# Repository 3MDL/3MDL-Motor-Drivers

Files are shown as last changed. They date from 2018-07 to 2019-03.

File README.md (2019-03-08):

# About #

This repository contains design files for low-cost brushed DC motor drivers. These low-cost motor drivers were concieved for use in low-cost swarm robotics. Work was done under the Mechanism, Mobility, and Multifunctional Design Laboratory (3MDL) at the University of Toledo.

## In This Repository ##

The Firmware sub folder contains test code that was used to evaluate motor drivers that were based on microcontrollers.

The Hardware sub folder contains hardware design files for:
* An OP Amp based current regulator motor driver
    * This design was confirmed to work and the cost is marginally lower than the off the shelf driver IC solution. However, due to complex timing, only limited testing was performed before the motor driver failed due to shoot through in the H bridge circuit.
* A Microcrocontroller based current regulator motor driver
    * The footprint used for the microcntroller was incorrect so this design could not be evaluated
* A motor driver using an off the shelf motor driver IC
    * This design was confirmed to work, however near the current limit rating of the driver IC, additional cooling is required or else the driver IC goes into over temperature protection mode.

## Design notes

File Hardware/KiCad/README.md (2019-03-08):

# KiCad Repository Info #

KiCad Modules are located in the MOD sub folder

KiCad Library parts are located in the LIB sub folder

Library and Modules used here are common with the [Thunkit Electronics KiCad Repository](https://github.com/cmccaskey/THUNKIT-KICAD)

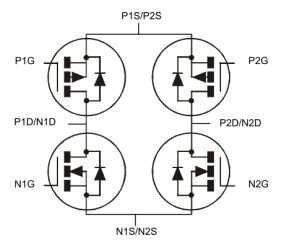
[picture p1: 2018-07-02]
Hardware/KiCad/MOD/DMHC3025LSD.png

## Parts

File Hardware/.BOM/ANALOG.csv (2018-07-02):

Id | Designator | Package | Quantity | Designation | Supplier and ref
1 | ,,,,,,,,,,,,,,,,,,,,,,,,,,,,,,,,,,,, | GND VIA | 37
2 | Q1,Q1,Q1 | SOIC-8_3.9x4.9mm_Pitch1.27mm | 3 | DMHC3025LSD
3 | C3,C4 | C_0603 | 2 | 10n
4 | P2,P5 | 100MIL_ST | 2 | PWR
5 | P3 | 100MIL_ST | 1 | VREF
6 | P4 | 100MIL_ST | 1 | DIR
7 | R1,R2,R3,R4,R5,R6,R7,R8,R11,R12 | R_0603 | 10 | 10K
8 | R9,R10 | R_0603 | 2 | 1K
9 | R13 | R_1812 | 1 | R
10 | U1 | SOIC-14_3.9x8.7mm_Pitch1.27mm | 1 | LM324
11 | U2 | SOIC-14_3.9x8.7mm_Pitch1.27mm | 1 | LM339
12 | P1 | 100MIL_ST | 1 | MOTOR
13 | C1,C2 | C_0603 | 2 | 0.1uF
14 | P6 | 100MIL_ST | 1 | PWM
15 | R14,R15 | R_0603 | 2 | 150

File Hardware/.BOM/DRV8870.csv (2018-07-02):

Id | Designator | Package | Quantity | Designation | Supplier and ref
1 | ,,,,,,,,, | GND VIA | 10
2 | U1 | HTSOP-8-1EP_3.9x4.9mm_Pitch1.27mm | 1 | DRV8870
3 | C1 | CP_Elec_6.3x7.7 | 1 | 47u
4 | C2 | C_0603 | 1 | 0.1u
5 | P1 | 100MIL_ST | 1 | PWR
6 | P2 | 100MIL_ST | 1 | DIR
7 | P3 | 100MIL_ST | 1 | VREF
8 | P4 | 100MIL_ST | 1 | MOTOR
9 | R1 | R_1812 | 1 | 0.1
Id | Designator | Package | Quantity | Designation | Supplier and ref
1 | ,,,,,,,,,,,,,,,, | GND VIA | 17
2 | C1 | C_0603 | 1 | 0.1uF
3 | C2,C3 | C_0603 | 2 | 22pF
4 | IC1 | QFN-24-1EP_4x4mm_Pitch0.5mm | 1 | ATTINY24A-M
5 | P1 | 100MIL_ST | 1 | MOTOR
6 | P2 | 100MIL_ST | 1 | VREF
7 | P3,P4 | 100MIL_ST | 2 | POWER
8 | P5 | Pin_Header_Straight_2x03_Pitch2.54mm | 1 | ICSP
9 | Q1 | SOIC-8_3.9x4.9mm_Pitch1.27mm | 1 | DMHC3025LSD
10 | Q2,Q3 | SOT-23 | 2 | Q_NMOS_DGS
11 | R1,R3,R4,R5 | R_0603 | 4 | 1K
12 | R2 | R_1812 | 1 | R
13 | Y1 | Crystal_HC49-U_Vertical | 1 | Crystal
Id | Designator | Package | Quantity | Designation | Supplier and ref
1 | ,,,,,,,,,,,,,,,,,,,,,,,,,,,,,,,,,,,, | GND VIA | 37
2 | Q1,Q1,Q1 | SOIC-8_3.9x4.9mm_Pitch1.27mm | 3 | DMHC3025LSD
3 | C3,C4 | C_0603 | 2 | 10n
4 | P2,P5 | 100MIL_ST | 2 | PWR
5 | P3 | 100MIL_ST | 1 | VREF
6 | P4 | 100MIL_ST | 1 | DIR
7 | R1,R2,R3,R4,R5,R6,R7,R8,R11,R12 | R_0603 | 10 | 10K
8 | R9,R10 | R_0603 | 2 | 1K
9 | R13 | R_1812 | 1 | R
10 | U1 | SOIC-14_3.9x8.7mm_Pitch1.27mm | 1 | LM324
11 | U2 | SOIC-14_3.9x8.7mm_Pitch1.27mm | 1 | LM339
12 | P1 | 100MIL_ST | 1 | MOTOR
13 | C1,C2 | C_0603 | 2 | 0.1uF
14 | P6 | 100MIL_ST | 1 | PWM
15 | R14,R15 | R_0603 | 2 | 150

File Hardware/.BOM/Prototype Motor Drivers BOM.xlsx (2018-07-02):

Designation | Kicad Package | Quantity | Digikey PN
0.05 Ohm Resistor | R_1812 | 10 | P50NBCT-ND
150 Ohm Resistor | R_0603 | 10 | RNCP0603FTD150RCT-ND
22pF Ceramic Capacitor | C_0603 | 10 | 732-7748-1-ND
10n Ceramic Capacitor | C_0603 | 10 | 732-7933-1-ND
0.1u Ceramic Capacitor | C_0603 | 10 | Can’t Find
47u Electrolytic Capacitor | CP_Elec_6.3x7.7 | 3 | PCE3908CT-ND
DMHC3025LSD MOSFET (H-Bridge) | SOIC-8_3.9x4.9mm_Pitch1.27mm | 10 | DMHC3025LSD-13DICT-ND
Q_NMOS_DGS MOSFET (NMOS) | SOT-23 | 10 | 2N7002-FDICT-ND
DRV8870 Motor Driver | HTSOP-8-1EP_3.9x4.9mm_Pitch1.27mm | 3 | 296-42660-1-ND
LM324 OP-Amp | SOIC-14_3.9x8.7mm_Pitch1.27mm | 3 | 497-1580-1-ND
LM339 Comparator | SOIC-14_3.9x8.7mm_Pitch1.27mm | 3 | 296-1013-1-ND
ATTINY24A-M Microcontroller | QFN-24-1EP_4x4mm_Pitch0.5mm | 3 | ATTINY24A-MURCT-ND

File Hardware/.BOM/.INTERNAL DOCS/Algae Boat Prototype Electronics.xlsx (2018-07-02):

M.I.M.E. Purchase Request
 | THE UNIVERSITY OF TOLEDO
 | Nitschke Hall Room 4005
 | Toledo, Ohio 43606 PH: (419) 530-8210 FAX: (419)-530-8206
 | ATTN: M.I.M.E. Budget Office
VENDOR: |  | Digi-Key |  |  | DATE: | 2018-07-02
ADDR 1: |  | 701 Brooks Avenue South
ADDR 2: |  |  |  |  | ACCOUNT # ITEMS WILL BE
C/S/Z: |  | Thief River Falls, MN 56701 |  |  | CHARGED TO: | 110780
PH: |  | 218-681-6674 |  |  | PICKUP or
FAX: |  |  |  |  | DELIVERY | Deliver
 | QUANTITY | CATALOG # | AND DESCRIPTION OF MATERIALS |  | Unit Cost | Total Cost
 | 10 | P50NBCT-ND | 0.05 Ohm Resistor |  | $0.63 | $6.32
 | 10 | RNCP0603FTD150RCT-ND | 150 Ohm Resistor |  | $0.03 | $0.30
 | 10 | 732-7748-1-ND | 22pF Ceramic Capacitor |  | $0.03 | $0.25
 | 10 | 732-7933-1-ND | 10n Ceramic Capacitor |  | $0.02 | $0.21
 | 3 | PCE3908CT-ND | 47u Electrolytic Capacitor |  | 0.38 | $1.14
 | 10 | DMHC3025LSD-13DICT-ND | DMHC3025LSD MOSFET (H-Bridge) |  | 0.912 | $9.12
 | 10 | 2N7002-FDICT-ND | Q_NMOS_DGS MOSFET (NMOS) |  | 0.163 | $1.63
 | 3 | 296-42660-1-ND | DRV8870 Motor Driver |  | 1.94 | $5.82
 | 3 | 497-1580-1-ND | LM324 OP-Amp |  | 0.36 | $1.08
 | 3 | 296-1013-1-ND | LM339 Comparator |  | 0.36 | $1.08
 | 3 | ATTINY24A-MURCT-ND | ATTINY24A-M Microcontroller |  | 0.76 | $2.28
 |  | Notes:
 |  |  | Shipping and Handling Charges
 |  |  |  | AUTOMATIC TOTAL WILL BE ENTERED |  | $29.23
* | Purchases under $2,500 can be faxed directly from the dept. budget office to the vendor.
* | Purchases over $2,500 need to be submitted to Purchasing via the dept. budget office.
* | Purchases that are grant related and over $2,000 must be approvaed by Grants Accounting via the dept. budget office.
* | Purchases that are over $10,000.00 need to go through bidding process via the dept. budget office.
 | Please complete all necessary information
 | in the areas above for all on or off campus |  |  | SUBMITTED BY:
 | purchase requests. Please e-mail the attached |  |  | Cameron McCaskey
 | form to kathryn.rose@utoledo.edu. Orders
 | will be processed the same day of receipt.

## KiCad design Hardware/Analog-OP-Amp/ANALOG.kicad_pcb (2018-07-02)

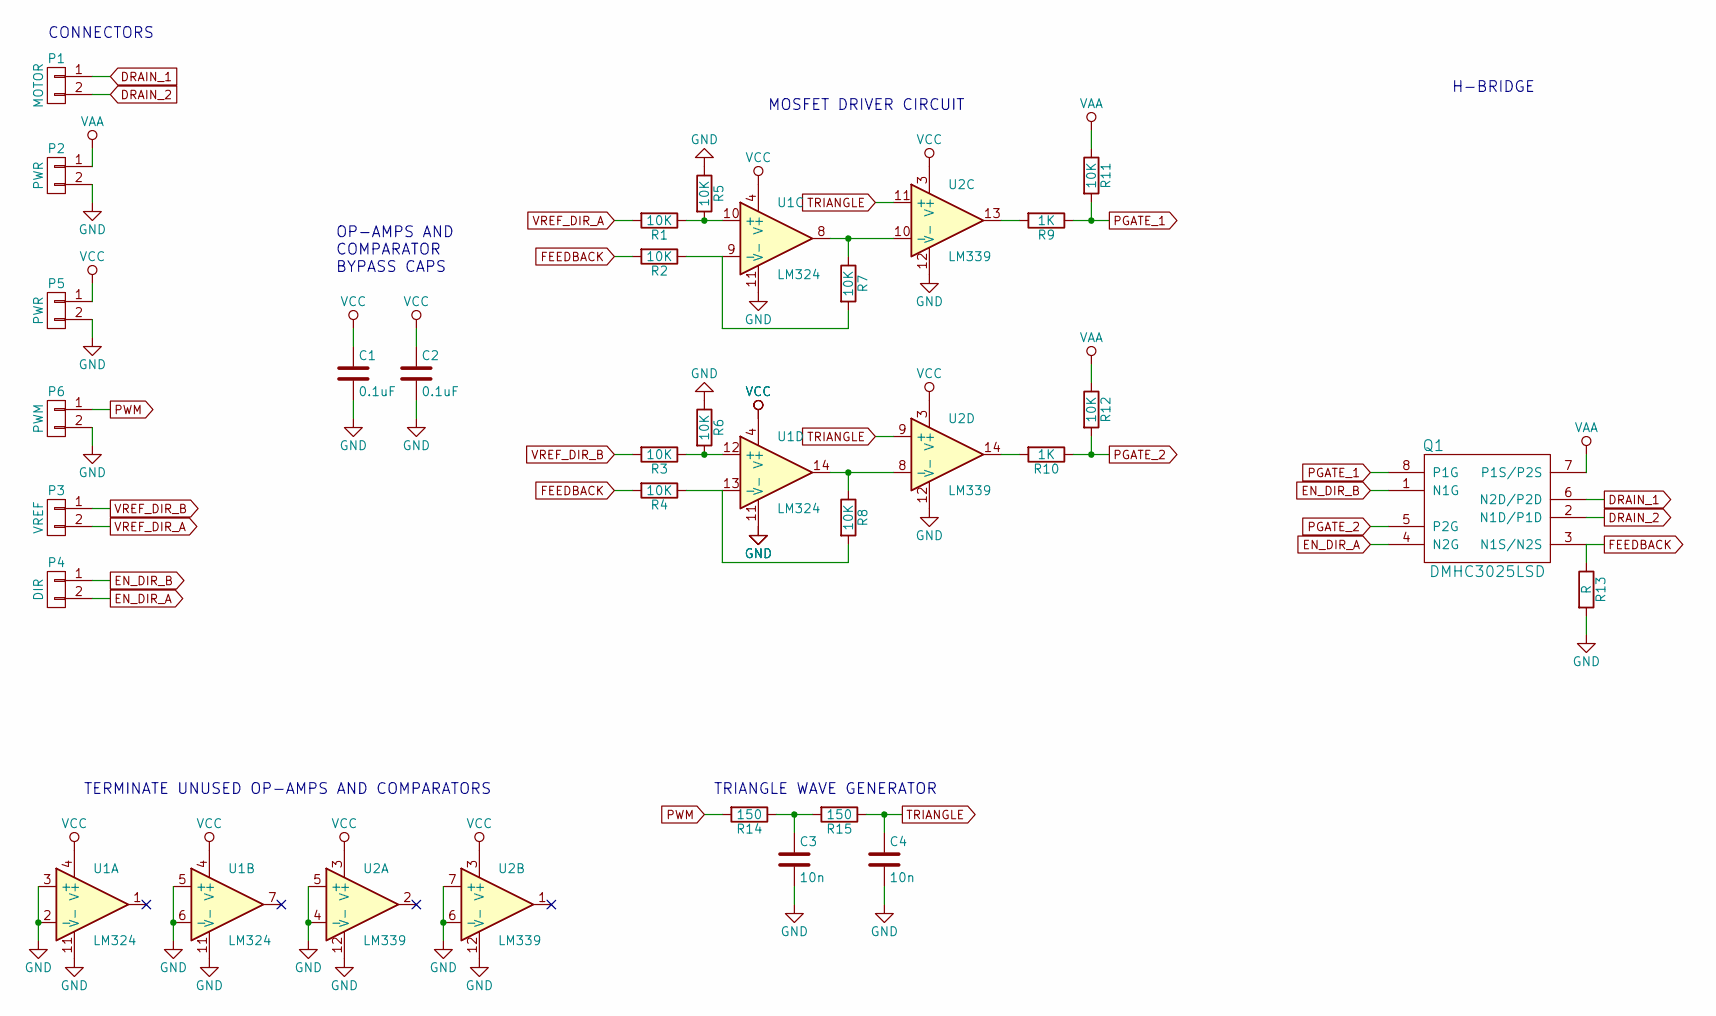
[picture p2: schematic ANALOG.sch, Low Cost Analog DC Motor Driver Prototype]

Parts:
C1, C2: 0.1uF; C_0603
C3, C4: 10n; C_0603
P1: MOTOR; 100MIL_ST
P2, P5: PWR; 100MIL_ST
P3: VREF; 100MIL_ST
P4: DIR; 100MIL_ST
P6: PWM; 100MIL_ST
Q1: DMHC3025LSD; SOIC-8_3.9x4.9mm_Pitch1.27mm
R1, R2, R3, R4, R5, R6, R7, R8, R11, R12: 10K; R_0603
R9, R10: 1K; R_0603
R13: R; R_1218
R14, R15: 150; R_0603
U1: LM324; SOIC-14_3.9x8.7mm_Pitch1.27mm
U2: LM339; SOIC-14_3.9x8.7mm_Pitch1.27mm

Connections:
DRAIN_1: P1.1, Q1.6 (N2D/P2D); also elsewhere on the board
DRAIN_2: P1.2, Q1.2 (N1D/P1D); also elsewhere on the board
EN_DIR_A: P4.2, Q1.4 (N2G); also elsewhere on the board
EN_DIR_B: P4.1, Q1.1 (N1G); also elsewhere on the board
FEEDBACK: Q1.3 (N1S/N2S), R2.2, R4.2, R13.1; also elsewhere on the board
GND: C1.2, C2.2, C3.2, C4.2, P2.2, P5.2, P6.2, R5.1, R6.1, R13.2, U1.2 (-), U1.3 (+), U1.5 (+), U1.6 (-), U1.11 (V-), U2.4 (-), U2.5 (+), U2.6 (-), U2.7 (+), U2.12 (V-)
unnamed: C3.1, R14.1, R15.2
unnamed: R1.1, R5.2, U1.10 (+)
unnamed: R2.1, R7.2, U1.9 (-)
unnamed: R3.1, R6.2, U1.12 (+)
unnamed: R4.1, R8.2, U1.13 (-)
unnamed: R7.1, U1.8, U2.10 (-)
unnamed: R8.1, U1.14, U2.8 (-)
unnamed: R9.2, U2.13
unnamed: R10.2, U2.14
PGATE_1: Q1.8 (P1G), R9.1, R11.2; also elsewhere on the board
PGATE_2: Q1.5 (P2G), R10.1, R12.2; also elsewhere on the board
PWM: P6.1, R14.2
TRIANGLE: C4.1, R15.1, U2.9 (+), U2.11 (+)
VAA: P2.1, Q1.7 (P1S/P2S), R11.1, R12.1; also elsewhere on the board
VCC: C1.1, C2.1, P5.1, U1.4 (V+), U2.3 (V+)
VREF_DIR_A: P3.2, R1.2
VREF_DIR_B: P3.1, R3.2

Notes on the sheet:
TERMINATE UNUSED OP-AMPS AND COMPARATORS
OP-AMPS AND COMPARATOR BYPASS CAPS
TRIANGLE WAVE GENERATOR
CONNECTORS
MOSFET DRIVER CIRCUIT
H-BRIDGE

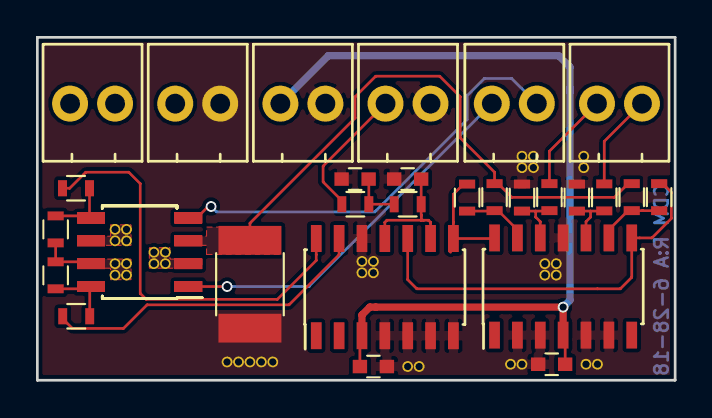
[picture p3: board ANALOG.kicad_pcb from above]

Board: 2 copper layers, 35.4 x 19.0 mm, 30 parts (0 on the bottom side), 23 nets.

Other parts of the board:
Q1#2, Q1#3: DMHC3025LSD; SOIC-8_3.9x4.9mm_Pitch1.27mm

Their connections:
DRAIN_1: Q1#2.6, Q1#3.6; also elsewhere on the board
DRAIN_2: Q1#2.2, Q1#3.2; also elsewhere on the board
EN_DIR_A: Q1#2.4, Q1#3.4; also elsewhere on the board
EN_DIR_B: Q1#2.1, Q1#3.1; also elsewhere on the board
FEEDBACK: Q1#2.3, Q1#3.3; also elsewhere on the board
PGATE_1: Q1#2.8, Q1#3.8; also elsewhere on the board
PGATE_2: Q1#2.5, Q1#3.5; also elsewhere on the board
VAA: Q1#2.7, Q1#3.7; also elsewhere on the board

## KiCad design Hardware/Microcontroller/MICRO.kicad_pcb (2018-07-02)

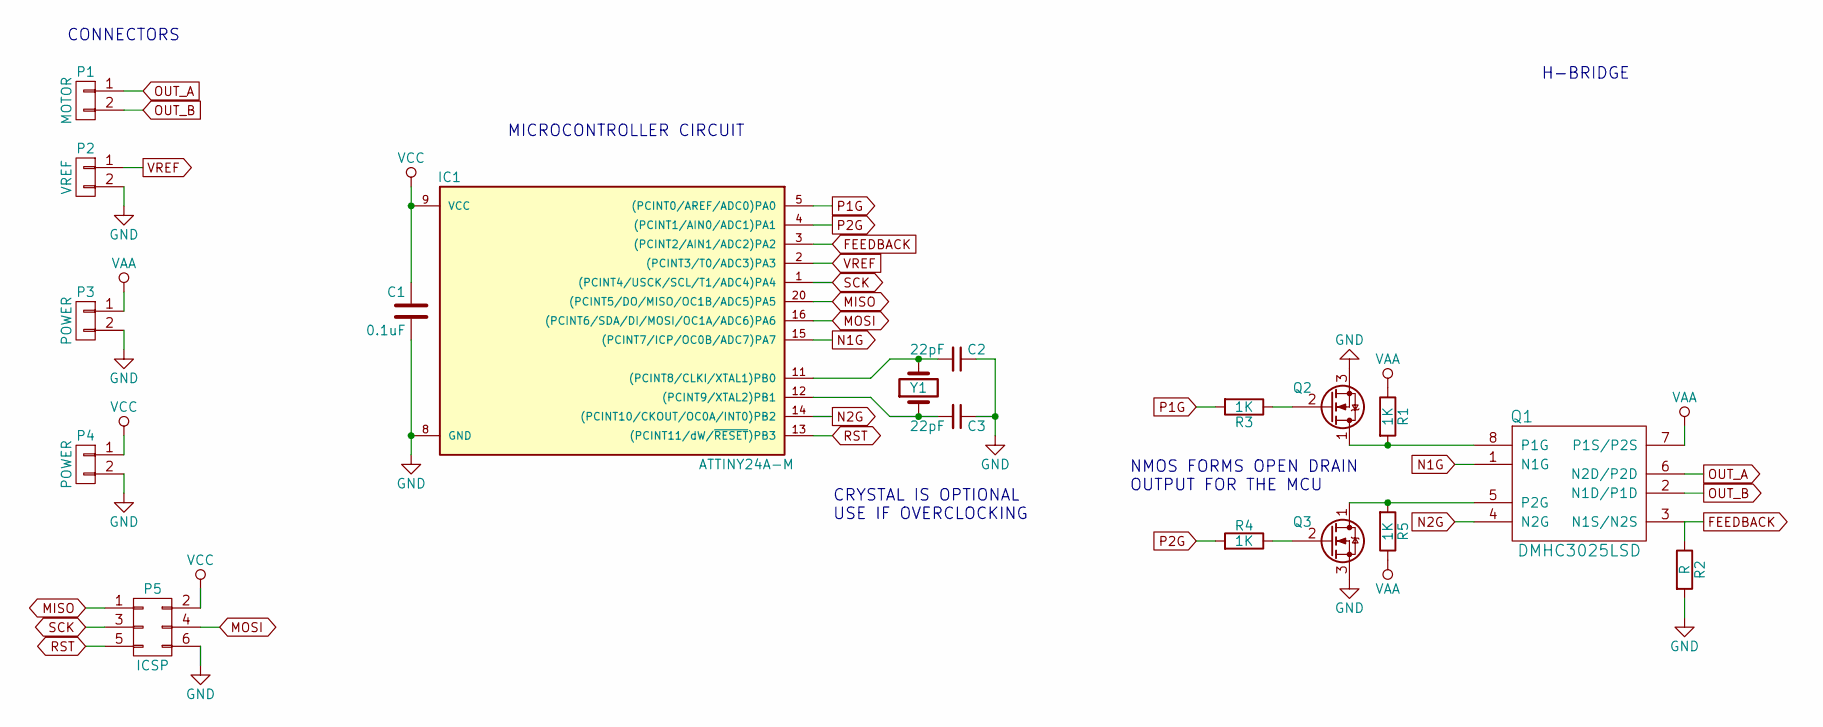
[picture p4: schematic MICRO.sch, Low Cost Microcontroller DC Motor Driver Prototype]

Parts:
C1: 0.1uF; C_0603
C2, C3: 22pF; C_0603
IC1: ATTINY24A-M; QFN-24-1EP_4x4mm_Pitch0.5mm
P1: MOTOR; 100MIL_ST
P2: VREF; 100MIL_ST
P3, P4: POWER; 100MIL_ST
P5: ICSP; Pin_Header_Straight_2x03_Pitch2.54mm
Q1: DMHC3025LSD; SOIC-8_3.9x4.9mm_Pitch1.27mm
Q2, Q3: Q_NMOS_DGS; SOT-23
R1, R3, R4, R5: 1K; R_0603
R2: R; R_1812
Y1: Crystal; Crystal_HC49-U_Vertical

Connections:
FEEDBACK: IC1.3 ((PCINT2/AIN1/ADC2)PA2), Q1.3 (N1S/N2S), R2.1
GND: C1.2, C2.1, C3.1, IC1.8 (GND), P2.2, P3.2, P4.2, P5.6, Q2.3 (S), Q3.3 (S), R2.2
MISO: IC1.20 ((PCINT5/DO/MISO/OC1B/ADC5)PA5), P5.1
MOSI: IC1.16 ((PCINT6/SDA/DI/MOSI/OC1A/ADC6)PA6), P5.4
N1G: IC1.15 ((PCINT7/ICP/OC0B/ADC7)PA7), Q1.1 (N1G)
N2G: IC1.14 ((PCINT10/CKOUT/OC0A/INT0)PB2), Q1.4 (N2G)
unnamed: C2.2, IC1.11 ((PCINT8/CLKI/XTAL1)PB0), Y1.2
unnamed: C3.2, IC1.12 ((PCINT9/XTAL2)PB1), Y1.1
unnamed: Q1.5 (P2G), Q3.1 (D), R5.2
unnamed: Q1.8 (P1G), Q2.1 (D), R1.2
unnamed: Q2.2 (G), R3.1
unnamed: Q3.2 (G), R4.1
OUT_A: P1.1, Q1.6 (N2D/P2D)
OUT_B: P1.2, Q1.2 (N1D/P1D)
P1G: IC1.5 ((PCINT0/AREF/ADC0)PA0), R3.2
P2G: IC1.4 ((PCINT1/AIN0/ADC1)PA1), R4.2
RST: IC1.13 ((PCINT11/dW/~RESET~)PB3), P5.5
SCK: IC1.1 ((PCINT4/USCK/SCL/T1/ADC4)PA4), P5.3
VAA: P3.1, Q1.7 (P1S/P2S), R1.1, R5.1
VCC: C1.1, IC1.9 (VCC), P4.1, P5.2
VREF: IC1.2 ((PCINT3/T0/ADC3)PA3), P2.1

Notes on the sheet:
CRYSTAL IS OPTIONAL USE IF OVERCLOCKING
NMOS FORMS OPEN DRAIN OUTPUT FOR THE MCU
H-BRIDGE
MICROCONTROLLER CIRCUIT
CONNECTORS

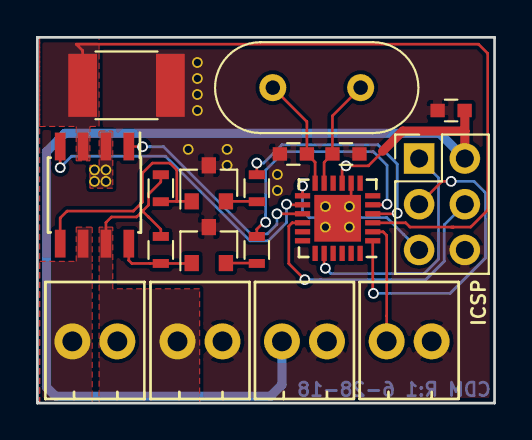
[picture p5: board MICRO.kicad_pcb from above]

Board: 2 copper layers, 25.4 x 20.3 mm, 18 parts (0 on the bottom side), 21 nets.

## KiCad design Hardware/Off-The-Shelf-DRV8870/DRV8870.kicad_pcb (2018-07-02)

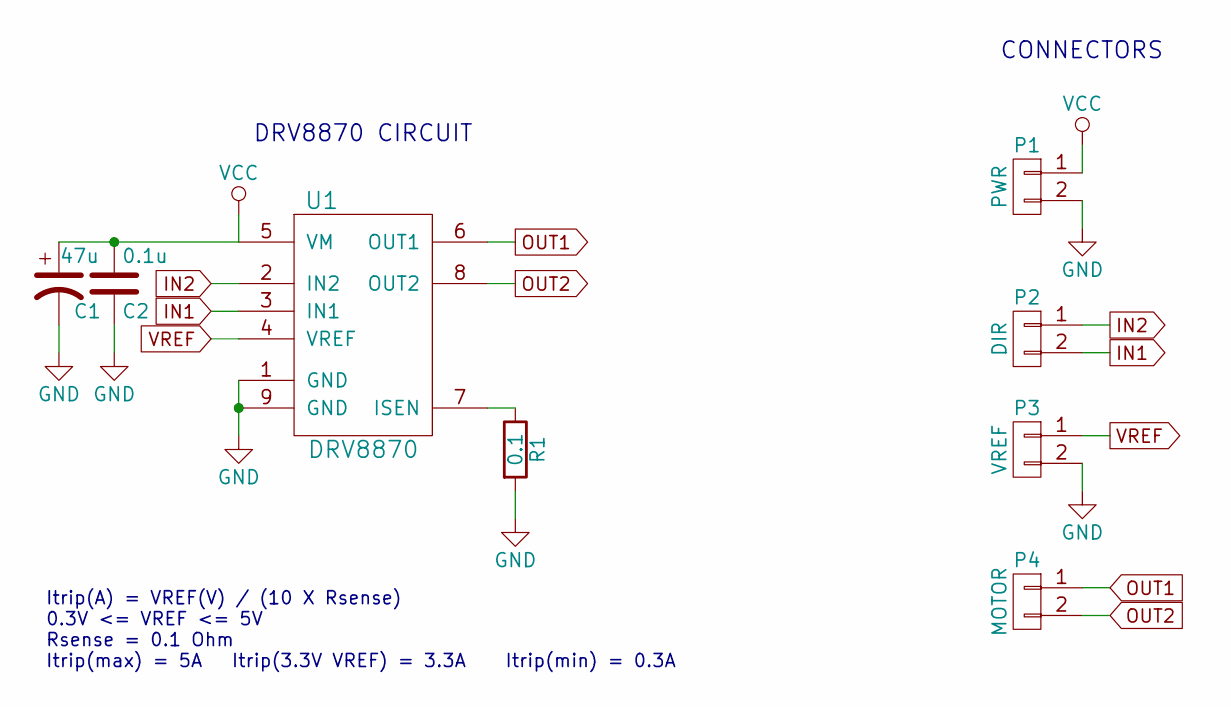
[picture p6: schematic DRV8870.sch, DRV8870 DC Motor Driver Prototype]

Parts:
C1: 47u; CP_Elec_6.3x7.7
C2: 0.1u; C_0603
P1: PWR; 100MIL_ST
P2: DIR; 100MIL_ST
P3: VREF; 100MIL_ST
P4: MOTOR; 100MIL_ST
R1: 0.1; R_1812
U1: DRV8870; HTSOP-8-1EP_3.9x4.9mm_Pitch1.27mm

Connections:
GND: C1.2, C2.1, P1.2, P3.2, R1.2, U1.1 (GND), U1.9 (GND)
IN1: P2.2, U1.3 (IN1)
IN2: P2.1, U1.2 (IN2)
unnamed: R1.1, U1.7 (ISEN)
OUT1: P4.1, U1.6 (OUT1)
OUT2: P4.2, U1.8 (OUT2)
VCC: C1.1, C2.2, P1.1, U1.5 (VM)
VREF: P3.1, U1.4 (VREF)

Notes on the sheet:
Itrip(A) = VREF(V) / (10 X Rsense) 0.3V <= VREF <= 5V Rsense = 0.1 Ohm Itrip(max) = 5A Itrip(3.3V VREF) = 3.3A Itrip(min) = 0.3A
CONNECTORS
DRV8870 CIRCUIT

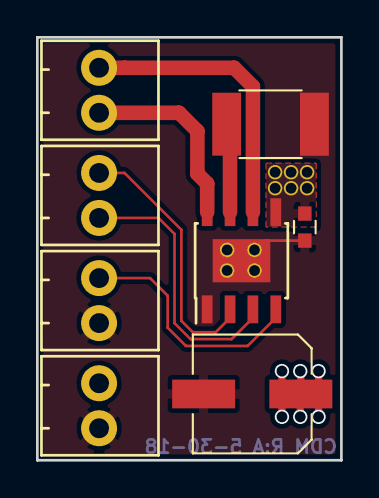
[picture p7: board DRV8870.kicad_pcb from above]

Board: 2 copper layers, 16.9 x 23.5 mm, 8 parts (0 on the bottom side), 8 nets.

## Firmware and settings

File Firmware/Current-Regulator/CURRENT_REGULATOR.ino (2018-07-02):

void setup() {
  pinMode(A0, OUTPUT);
  pinMode(A1, INPUT);
  pinMode(A2, INPUT);
  pinMode(13, OUTPUT);
}


void loop() {
  digitalWrite(A0, LOW);
  digitalWrite(13, LOW);
  if (analogRead(A1) > analogRead(A2)){
    digitalWrite(A0, LOW);
    digitalWrite(13, LOW);
  } else {
    digitalWrite(A0, HIGH);
    digitalWrite(13, HIGH);
  }
}

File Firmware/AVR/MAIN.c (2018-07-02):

#define F_CPU 800000UL
#define delay 10

#include <avr/io.h>
#include <util/delay.h>

#define voltage 0.08
#define voltageADC (voltage*1024.0)/5.0

//PB3 is digital switch output
//PB4 is ADC feedback input

int main() {
	ADCSRA |= (1 << ADEN); //enable ADC
	DDRB |= (1 << PB3) | (1 << PB2); //PB2 & PB3 output
	ADMUX = (1 << MUX1);// | (1 << REFS1); //A1 with 1.1V internal ref
  while (1) {
		ADCSRA |= (1 << ADSC); //start reading

		while (ADCSRA & (1 << ADSC));
		int adcLow = ADCL;
		int adcHigh = ADCH;
		float adcVal = (adcHigh << 8) | adcLow;

		if (adcVal > 10){
			PORTB &= ~(1 << PB3); //turn switch OFF
		} else {
			PORTB |= (1 << PB3); //turn switch ON
		}	
		PINB = (1 << PB2); //toggle PB2 to measure freq.
		//_delay_us(delay);
  }
}
